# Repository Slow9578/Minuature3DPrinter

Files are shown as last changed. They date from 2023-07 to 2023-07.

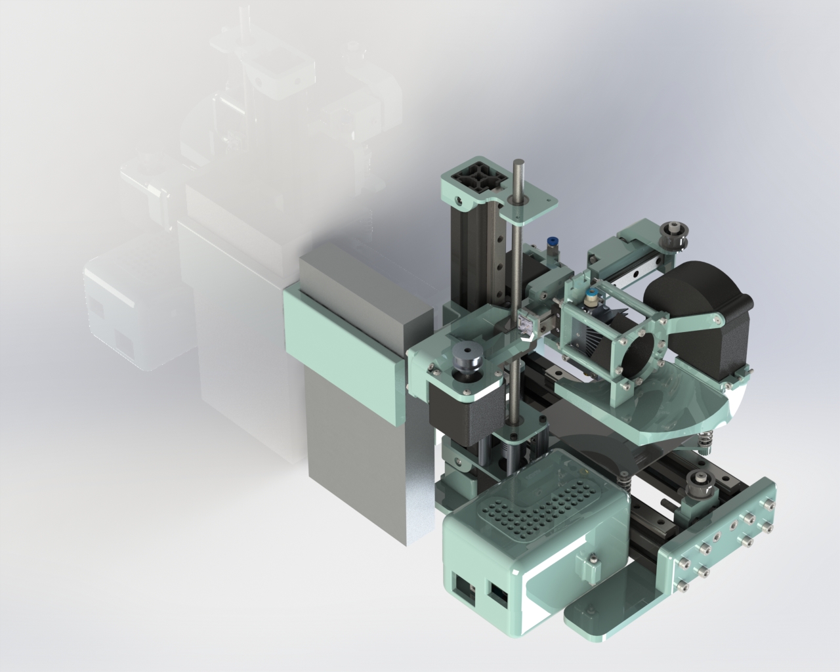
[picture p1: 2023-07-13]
FullCADRenders/PrinterOrthographicView.JPG

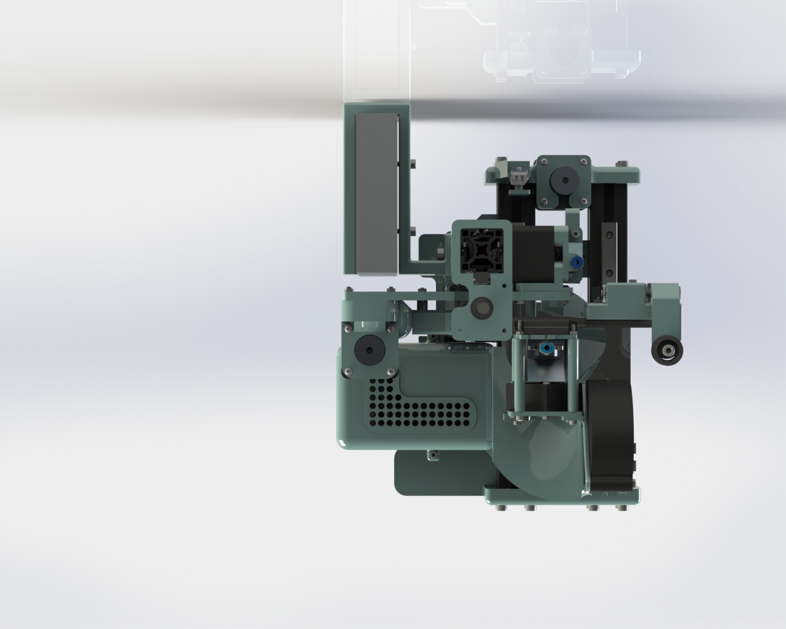
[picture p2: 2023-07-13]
FullCADRenders/PrinterTopView.JPG

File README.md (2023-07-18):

# Minuature3DPrinter
A minuature 3D Printer created for learning more about the inner workings of 3D printers

Due to size constraints the full Solidworks Assembly can be found here:https://drive.google.com/drive/folders/1Yb2QYuJ1OSHzWRYjtjEfcz5mn8uoaapG?usp=sharing

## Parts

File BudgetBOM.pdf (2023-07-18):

Part # | Component | Description | Quantity | Cost Per Unit | Total Cost
HE1A | MK8 HotEnd (https://www.amazon.com/Creality-3D-Assembled-Extruder-Capricorn/dp/B07WNQP916) | Pre-assembled Ender 3 hot end | 1 | 19 | 19
HE2A | Heat Break Fan (https://www.digikey.com/en/products/detail/cui-devices/CFM-4020CF-235-114/15765096) | FAN AXIAL 40X20MM 24VDC WIRE 4.4 CFM | 1 | 6 | 6
HE3A | Print Fan (https://www.amazon.com/Creality-Original-40x40x10MM-Extruder-Printer/dp/B07GXPJB25) | Ender 3 Stock Print Fan | 1 | 9 | 9
HE4A | Mini Heated Bed (https://openbuildspartstore.com/mini-heated-bed/) | 100mm x 100mm 24/12V Openbuild Heated Bed | 1 | 10.99 | 10.99
HE5A | Bed Thermistor (https://www.digikey.com/en/products/detail/littelfuse-inc/GL104R5J/7325040) | THERM NTC 100KOHM 4263K BEAD | 1 | 1.19 | 1.19
HE6A | Bowden Tube (https://www.amazon.com/Creality-Capricorn-Filament-Extruder-Fitting/dp/B09GM6W972) | Bowden PTFE Tube for 1.75mm Filament with Fittings | 1 | 11.45 | 11.45
HW1 | Z-Axis 3030 Aluminum Extrusion (https://www.amazon.com/gp/product/B09FPBK5SP/ref=ox_sc_act_title_1?smid=A2J4PW8EKV80FA&psc=1) | 288.5mm Long, Black Anodized | 1 | 6.66 | 6.66
HW2 | Y-Axis 3030 Aluminum Extrusion (https://www.amazon.com/gp/product/B09FPBK5SP/ref=ox_sc_act_title_1?smid=A2J4PW8EKV80FA&psc=1) | 261mm Long, Black Anodized | 2 | 6.66 | 13.33
HW3 | MGN12H Linear Rail (https://www.amazon.com/gp/product/B08B348GZ9/ref=ox_sc_act_title_2?smid=A1RTFVCI20VZT2&th=1) | 200mm Long | 4 | 13.99 | 55.96
HW4 | 8mm Metric Acme Lead Screw (https://openbuildspartstore.com/8mm-metric-acme-lead-screw/) | 290mm long | 1 | 10.99 | 10.99
HW5 | Anti-Backlash Nut Block (https://openbuildspartstore.com/anti-backlash-nut-block-for-8mm-metric-acme-lead-screw/) | For 8mm Metric Acme Lead Screw | 1 | 9.99 | 9.99
HW6 | 5mm * 8mm Flexible Coupling (https://openbuildspartstore.com/5mm-8mm-flexible-coupling/) | For 8mm Metric Acme Lead Screw | 1 | 6.99 | 6.99
HW7 | Flanged Bearing (https://openbuildspartstore.com/flanged-bearing-688zz-8x16x5/) | 688ZZ 8x16x5 | 2 | 1.5 | 3
HW8 | Timing Belt (https://openbuildspartstore.com/gt2-2m-timing-belt-by-the-foot/) | GT2-2M, 5 Ft. | 1 | 12.45 | 12.45
HW9 | Belt Crimps (https://www.amazon.com/dp/B0968D2GR5?psc=1&ref=ppx_yo2ov_dt_b_product_details) | Copper | 4 | 2.5 | 10
HW10 | Smooth Idler Pulley (https://openbuildspartstore.com/smooth-idler-pulley-kit/) | OD: 22mm ID: 16mm Width: 12.7mm | 2 | 5.99 | 11.98
HW11 | Extruder Drive Gear (https://www.amazon.com/dp/B01J5ON2Y2?psc=1&ref=ppx_yo2ov_dt_b_product_details) | 36Teeth Bore 5mm Stainless Steel Drive Gear | 1 | 6.99 | 6.99
HW12 | Timing Pulley Gear (https://openbuildspartstore.com/gt2-2m-timing-pulley-30-tooth/) | 30 Tooth GT2-2M | 2 | 6.99 | 13.98
HW13 | Bearing Block Spacer (https://openbuildspartstore.com/aluminum-spacers-10-pack/) | M5 ID, 40mm,10mm OD, Aluminum | 4 | 1.5 | 6
HW14 | Extruder Idler Bearing (https://www.amazon.com/uxcell-U604ZZ-Bearings-4mmx13mmx4mm-Shielded/dp/B082PSVNW8?s=industrial) | 4mmx13mmx4mm Double Metal Shielded Carbon Steel Bearings | 1 | 0.66 | 8
E1A | RAMPS 1.4 Sheild (https://www.amazon.com/dp/B01E5K98C6?s=electronics&sp_csd=d2lkZ2V0TmFtZT1zcF9kZXRhaWxfdGhlbWF0aWM) | Shield For Arduino Mega | 1 | 10 | 10
E2A | Arduino Mega (https://www.amazon.com/dp/B08V4RCRS2?psc=1&ref=ppx_yo2ov_dt_b_product_details) | Mega 2560 5V | 1 | 20.99 | 20.99
E3A | 24V Meanwell Power Supply (https://www.mouser.com/ProductDetail/MEAN-WELL/LRS-350-24?qs=ah3jBNVE1PT%252BkwLcackrGA%3D%3D) | LRS-350-24, 24V/14.6A MeanWell Power Suppy | 1 | 37.52 | 37.52
E4A | Stepper Motor Driver (https://www.amazon.com/HiLetgo-Stepstick-Stepper-Printer-Compatible/dp/B07BND65C8?hvadid=616863377916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) | A4988 clones, 5 drivers and 5 heatsinks per 10$ | 4 | 2 | 10
E5A | End Stop Switches (https://mechanicalkeyboards.com/shop/index.php?l=product_detail&p=4117&dqty=1) | Kailh BOX Black Switches Plate Mount - Linear | 3 | 1.16 | 3.5
E6A | Stepper Motor (https://www.amazon.com/Creality-Official-3D-Compatible-axis%EF%BC%88D-Shape%EF%BC%89/dp/B09L5M63B1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) | 42-40 Stepper Motor, 2 Phase 1A 1.8 Degree 0.4 N.M | 4 | 13 | 52
E7A | JST 2Pin Connector Female (https://www.amazon.com/daier-Micro-2-Pin-Connector-Female/dp/B01DUC1O68) | Amazon, 20pcs per 8.99$ | 7 | 0.45 | 8.99
E8A | Stepper Motor Cabels (https://www.amazon.com/Stepper-Cables-Terminal-Paralled-Printer/dp/B08LD14CHS?sp_csd=d2lkZ2V0TmFtZT1zcF9hdGY) | Amazon, 6pcs per 11$ | 4 | 1.83 | 11
P1 | X-AxisBackPlate (https://www.amazon.com/dp/B08ZB48FJM?psc=1&ref=ppx_yo2ov_dt_b_product_details) | 41g PETG, 0.8mm nozzle, 20% infill | 1 | 1.03 | 1.03
P2 | X-AxisMotorFixture (https://www.amazon.com/dp/B08ZB48FJM?psc=1&ref=ppx_yo2ov_dt_b_product_details) | 31g PETG, 0.8mm nozzle, 20% infill | 1 | 0.78 | 0.78
P3A | HotEndBackPlate (https://www.amazon.com/dp/B08ZB48FJM?psc=1&ref=ppx_yo2ov_dt_b_product_details) | 8g PETG, 0.8mm nozzle, 20% infill | 1 | 0.2 | 0.2
P4 | HotEndFrontPlate (https://www.amazon.com/dp/B08ZB48FJM?psc=1&ref=ppx_yo2ov_dt_b_product_details) | 6g PETG, 0.8mm nozzle, 20% infill | 1 | 0.15 | 0.15
P5 | X-AxisBackPlateSpacer (https://www.amazon.com/dp/B08ZB48FJM?psc=1&ref=ppx_yo2ov_dt_b_product_details) | 1g PETG, 0.8mm nozzle, 20% infill | 2 | 0.03 | 0.06

P6 | X-AxisTensionerBase (https://www.amazon.com/dp/B08ZB48FJM?psc=1&ref=ppx_yo2ov_dt_b_product_details) | 40g PETG, 0.8mm nozzle, 20% infill | 1 | 1 | 1
P7 | Y-AxisRailConnectingPlate (https://www.amazon.com/dp/B08ZB48FJM?psc=1&ref=ppx_yo2ov_dt_b_product_details) | 14g PETG, 0.8mm nozzle, 20% infill | 1 | 0.35 | 0.35
P8 | BedBasePlate (https://www.amazon.com/dp/B08ZB48FJM?psc=1&ref=ppx_yo2ov_dt_b_product_details) | 27g PETG, 0.8mm nozzle, 20% infill | 1 | 0.68 | 0.68
P9 | LevelingKnob (https://www.amazon.com/dp/B08ZB48FJM?psc=1&ref=ppx_yo2ov_dt_b_product_details) | 1g PETG, 0.8mm nozzle, 20% infill | 4 | 0.03 | 0.12
P10 | Y-AxisFrontPlate (https://www.amazon.com/dp/B08ZB48FJM?psc=1&ref=ppx_yo2ov_dt_b_product_details) | 42g PETG, 0.8mm nozzle, 20% infill | 1 | 1.05 | 1.05
P11 | BearingPillowBlockPlate (https://www.amazon.com/dp/B08ZB48FJM?psc=1&ref=ppx_yo2ov_dt_b_product_details) | 5g PETG, 0.8mm nozzle, 20% infill | 1 | 0.13 | 0.13
P12 | Z-AxisMotorFixture (https://www.amazon.com/dp/B08ZB48FJM?psc=1&ref=ppx_yo2ov_dt_b_product_details) | 16g PETG, 0.8mm nozzle, 20% infill | 1 | 0.4 | 0.4
P13 | LeadScrewBearingFixture (https://www.amazon.com/dp/B08ZB48FJM?psc=1&ref=ppx_yo2ov_dt_b_product_details) | 16g PETG, 0.8mm nozzle, 20% infill | 1 | 0.4 | 0.4
P14 | Y-AxisRearPlate (https://www.amazon.com/dp/B08ZB48FJM?psc=1&ref=ppx_yo2ov_dt_b_product_details) | 54g PETG, 0.8mm nozzle, 20% infill | 1 | 1.35 | 1.35
P15 | X-AxisTensioner (https://www.amazon.com/dp/B08ZB48FJM?psc=1&ref=ppx_yo2ov_dt_b_product_details) | 13g PETG, 0.8mm nozzle, 20% infill | 1 | 0.33 | 0.33
P16 | ExtruderMotorFixture (https://www.amazon.com/dp/B08ZB48FJM?psc=1&ref=ppx_yo2ov_dt_b_product_details) | 25g PETG, 0.8mm nozzle, 20% infill | 1 | 0.63 | 0.63
P17 | PowerSupplyMountingPlate (https://www.amazon.com/dp/B08ZB48FJM?psc=1&ref=ppx_yo2ov_dt_b_product_details) | 126g PETG, 0.8mm nozzle, 20% infill | 1 | 3.15 | 3.15
P18 | Y-AxisTensioner (https://www.amazon.com/dp/B08ZB48FJM?psc=1&ref=ppx_yo2ov_dt_b_product_details) | 10g PETG, 0.8mm nozzle, 20% infill | 1 | 0.25 | 0.25
P19 | Y-AxisBeltAnchor (https://www.amazon.com/dp/B08ZB48FJM?psc=1&ref=ppx_yo2ov_dt_b_product_details) | 2g PETG, 0.8mm nozzle, 20% infill | 1 | 0.05 | 0.05
P20 | X-AxisEndStop (https://www.amazon.com/dp/B08ZB48FJM?psc=1&ref=ppx_yo2ov_dt_b_product_details) | 5g PETG, 0.8mm nozzle, 20% infill | 1 | 0.13 | 0.13
P21 | HotEndSpacer (https://www.amazon.com/dp/B08ZB48FJM?psc=1&ref=ppx_yo2ov_dt_b_product_details) | 3g PETG, 0.8mm nozzle, 20% infill | 4 | 0.08 | 0.32
P22 | Z-AxisBasePlate (https://www.amazon.com/dp/B08ZB48FJM?psc=1&ref=ppx_yo2ov_dt_b_product_details) | 70g PETG, 0.8mm nozzle, 20% infill | 1 | 1.75 | 1.75
P23A | PrintFanFixture (https://www.amazon.com/dp/B08ZB48FJM?psc=1&ref=ppx_yo2ov_dt_b_product_details) | 6g PETG, 0.8mm nozzle, 20% infill | 1 | 0.15 | 0.15
P25 | Z-AxisEndStopFixture (https://www.amazon.com/dp/B08ZB48FJM?psc=1&ref=ppx_yo2ov_dt_b_product_details) | 3g PETG, 0.8mm nozzle, 20% infill | 1 | 0.08 | 0.08
P26 | Y-AxisEndStopFixture (https://www.amazon.com/dp/B08ZB48FJM?psc=1&ref=ppx_yo2ov_dt_b_product_details) | 10g PETG, 0.8mm nozzle, 20% infill | 1 | 0.25 | 0.25
P27 | FrontBasePlate (https://www.amazon.com/dp/B08ZB48FJM?psc=1&ref=ppx_yo2ov_dt_b_product_details) | 50g PETG, 0.8mm nozzle, 20% infill | 1 | 1.25 | 1.25
P28 | ArduinoCaseBottom (https://www.amazon.com/dp/B08ZB48FJM?psc=1&ref=ppx_yo2ov_dt_b_product_details) | 119g PETG, 0.8mm nozzle, 20% infill | 1 | 2.98 | 2.98
P29 | ArduinoCaseTop (https://www.amazon.com/dp/B08ZB48FJM?psc=1&ref=ppx_yo2ov_dt_b_product_details) | 117g PETG, 0.8mm nozzle, 20% infill | 1 | 2.93 | 2.93
P30 | ArduinoCaseGrate (https://www.amazon.com/dp/B08ZB48FJM?psc=1&ref=ppx_yo2ov_dt_b_product_details) | 10g PETG, 0.8mm nozzle, 20% infill | 1 | 0.25 | 0.25
P31 | Y-Z-AxisConnectingBracket (https://www.amazon.com/dp/B08ZB48FJM?psc=1&ref=ppx_yo2ov_dt_b_product_details) | 7g PETG, 0.8mm nozzle, 20% infill | 1 | 0.18 | 0.18
P32 | ExtruderLever (https://www.amazon.com/dp/B08ZB48FJM?psc=1&ref=ppx_yo2ov_dt_b_product_details) | 7g PETG, 0.8mm nozzle, 20% infill | 1 | 0.18 | 0.18
P33 | ExtruderPlate (https://www.amazon.com/dp/B08ZB48FJM?psc=1&ref=ppx_yo2ov_dt_b_product_details) | 11g PETG, 0.8mm nozzle, 20% infill | 1 | 0.28 | 0.28
P34 | ExtruderSpringEndstop (https://www.amazon.com/dp/B08ZB48FJM?psc=1&ref=ppx_yo2ov_dt_b_product_details) | 1g PETG, 0.8mm nozzle, 20% infill | 1 | 0.03 | 0.03
P35 | EndStopCap (https://www.amazon.com/dp/B08ZB48FJM?psc=1&ref=ppx_yo2ov_dt_b_product_details) | 2g PETG, 0.8mm nozzle, 20% infill | 1 | 0.05 | 0.05
P36 | BacklashNutSpacer (https://www.amazon.com/dp/B08ZB48FJM?psc=1&ref=ppx_yo2ov_dt_b_product_details) | 1g PETG, 0.8mm nozzle, 20% infill | 2 | 0.03 | 0.06
F1A | M3 Socket Head Kit (https://www.amazon.com/1110pcs-Stainless-Washers-Assortment-Precise/dp/B08YYZSZVP) | Contains required fastners F1-F6 and F20 | 1 | 19 | 19
F7 | M3x45mm Socket Head (https://openbuildspartstore.com/m3-cap-head-screws/) | Openbuilds, 1 pc per 0.29$ | 4 | 0.29 | 1.16
F8 | M3x70mm Socket Head (https://www.amazon.com/XunLiu-Socket-Screws-Wrench-Knurled/dp/B07CHKP6F3) | amazon, 10pcs per 8$ | 4 | 1.25 | 8
F2A | M3 Flat Head Kit (https://www.amazon.com/iExcell-Thread-Socket-Screws-Assortment/dp/B08JKCXP9X) | Contains required fastners F9-F12 | 8 | 0.05 | 5.45

F3A | M3 Button Head Kit (https://www.amazon.com/VIGRUE-570PCS-Stainless-Assortment-Machine/dp/B08H24W42K?s=industrial) | Contains required fastners F13-F17 | 1 | 16 | 16
F18 | M3 Set Screw 6mm (https://www.mcmaster.com/91390A100/) | McMaster-Carr:91390A100, $6.52 per pack of 100 | 5 | 0.07 | 6.52
F19 | M3 Tnut (https://openbuildspartstore.com/tee-nuts-m3-10-pack/) | Openbuilds, 10 pcs per 2.79$ | 33 | 0.28 | 11.16
F21 | M4x12mm Socket Head (https://www.amazon.com/M4-0-70-Socket-Screws-Marine-Stainless/dp/B07DVPC7HT) | Amazon, 10pcs per 5.45$ | 2 | 0.55 | 5.45
F22 | M5x6mm Socket Head (https://www.amazon.com/uxcell-M5x6mm-Stainless-Metric-Fasteners/dp/B01IXZ2SSA) | Amazon, 25 pcs per 10$ | 18 | 0.25 | 10
F23 | M5x8mm Socket Head (https://www.amazon.com/Socket-Screws-DIN912-Stainless-M5x18mm/dp/B083DZBVV1) | Amazon, 10pcs per 8$ | 2 | 0.8 | 8
F24 | M5x12mm Socket Head (https://www.amazon.com/Socket-Screws-DIN912-Stainless-M5x18mm/dp/B083DYLJ1S) | Amazon, 10pcs per 8$ | 2 | 0.8 | 8
F25 | M5x18mm Socket Head (https://www.amazon.com/Socket-Screws-DIN912-Stainless-M5x18mm/dp/B083DZDQTH) | Amazon, 10pcs per 8$ | 1 | 0.8 | 8
F26 | M5x40mm LowProfile (https://openbuildspartstore.com/low-profile-screws-m5-10-pack-/) | Openbuilds, 1pcs per 1.69$ | 1 | 1.69 | 1.69
F27 | M5x10mm Flat Head (https://www.amazon.com/METALLIXITY-Countersunk-Machine-M5x10mm-Stainless/dp/B09Y5P8T7W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) | Amazon, 20pcs per 7$ | 1 | 0.35 | 7
F28 | M5x18mm Flat Head (https://www.amazon.com/uxcell-Security-Stainless-Countersunk-Fasteners/dp/B0BC8K7Q1C) | Amazon, 20pcs per 7.50$ | 1 | 0.38 | 7.5
F29 | M5 Tnut (https://openbuildspartstore.com/tee-nuts-m5-10-pack/) | Openbuilds, 10 pcs per $2.99 | 8 | 0.3 | 2.99
F30 | M5 Nut (https://www.mcmaster.com/90592A095/) | McMaster-Carr:90592A095, $4.05 per pack of 100 | 2 | 0.04 | 4.05
F31 | M6x50mm Socket Head (https://www.mcmaster.com/91290A207/) | McMaster-Carr:91290A207, $5.52 per pack of 5 | 4 | 1.1 | 5.52
F32 | M6 Nut (https://www.mcmaster.com/90591A151/) | McMaster-Carr:90591A151, $3.14 per pack of 100 | 4 | 0.03 | 3.14
F33 | Ender3 Bed Spring (https://www.amazon.com/dp/B07FY47BX7?s=industrial&sp_csd=d2lkZ2V0TmFtZT1zcF9kZXRhaWw) | Amazon, 20pcs per 8.99$ | 9 | 0.45 | 8.99
F34 | M3 Heat Inserts (https://www.amazon.com/M3x4-0mm-OD4-6mm-Staking-Threaded-Quik-Tek/dp/B08T7M2H4S) | 100pcs/lot M3x4.0mm, OD4.6mm | 7 | 0.12 | 12
| | | | Total | 570.55

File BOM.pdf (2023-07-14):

Part # | Component | Description | Quantity | Cost Per Unit | Total Cost
HE1 | Aluminum Bar (https://www.mcmaster.com/8975K11-8975K707/) | Multipurpose 6061 Aluminum 1/2" Thick x 1" Wide x 6" Long | 1 | 4.92 | 4.92
HE2 | Volcano nozzle (https://e3d-online.com/products/volcano-nozzles?variant=40924170256443) | Brass E3D Volcano Nozzle 1.75mm in 1.2mm out | 1 | 7.1 | 7.1
HE3 | Heater Cartridge (https://e3d-online.com/products/high-precision-heater-cartridges?variant=31134327504955) | 24V, 40W, E3D High Precision Heater Cartridges | 2 | 20 | 40
HE4 | Heat Sink (https://www.digikey.com/en/products/detail/ohmite/BGAH270-175E/11561718) | BGAH270-175E Heat Sink, 3.5 C/W Natural Thermal Resistance | 1 | 6.61 | 6.61
HE5 | Silicon Casting Kit (https://www.amazon.com/gp/product/B08CVQJ4YD/ref=ppx_yo_dt_b_asin_title_o08_s00?ie=UTF8&psc=1) | Platinum Liquid Silicone for Mold Making | 1 | 34 | 34
HE6 | Heat Break (https://www.amazon.com/gp/product/B09V46R7YR/ref=ppx_yo_dt_b_asin_title_o05_s00?ie=UTF8&psc=1) | Bimetal Heatbreak Titanium Alloy and Copper | 1 | 8.99 | 8.99
HE7 | Bowden Tube (https://www.amazon.com/Creality-Capricorn-Filament-Extruder-Fitting/dp/B09GM6W972) | Bowden PTFE Tube for 1.75mm Filament with Fittings | 1 | 11.45 | 11.45
HE8 | Thermal Paste (https://www.amazon.com/Performance-Ultra-Low-Impedance-Heatsink-Compound/dp/B07KQ1T158) | Corsair TM30 Performance Thermal Paste 0.029 C/W | 1 | 7.99 | 7.99
HE9 | Heat Break Fan (https://www.digikey.com/en/products/detail/cui-devices/CFM-4020CF-235-114/15765096) | FAN AXIAL 40X20MM 24VDC WIRE 4.4 CFM | 1 | 6 | 6
HE10 | Print Fan (https://www.digikey.com/en/products/detail/mechatronics-fan-group/B7530E24B-BSR/5209737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) | FAN BLOWER 76X30MM 24VDC WIRE, B7530E24B-BSR | 1 | 15.8 | 15.8
HE11 | Hot End Thermistor (https://e3d-online.com/products/thermistor-cartridge?_pos=1&_psq=thermi&_ss=e&_v=1.0) | E3D Semitec 104NT Cartridge | 1 | 7 | 7
HE12 | Mini Heated Bed (https://openbuildspartstore.com/mini-heated-bed/) | 100mm x 100mm 24/12V Openbuild Heated Bed | 1 | 10.99 | 10.99
HE13 | PEI Sheet (https://www.amazon.com/gp/product/B07C3GYHYM/ref=ppx_od_dt_b_asin_title_s00?ie=UTF8&psc=1) | Gizmo Dorks PEI Sheet 5" x 5.5" | 1 | 12 | 12
HE14 | Bed Thermistor (https://www.digikey.com/en/products/detail/littelfuse-inc/GL104R5J/7325040) | THERM NTC 100KOHM 4263K BEAD | 1 | 1.19 | 1.19
HW1 | Z-Axis 3030 Aluminum Extrusion (https://www.amazon.com/gp/product/B09FPBK5SP/ref=ox_sc_act_title_1?smid=A2J4PW8EKV80FA&psc=1) | 288.5mm Long, Black Anodized | 1 | 6.66 | 6.66
HW2 | Y-Axis 3030 Aluminum Extrusion (https://www.amazon.com/gp/product/B09FPBK5SP/ref=ox_sc_act_title_1?smid=A2J4PW8EKV80FA&psc=1) | 261mm Long, Black Anodized | 2 | 6.66 | 13.33
HW3 | MGN12H Linear Rail (https://www.amazon.com/gp/product/B08B348GZ9/ref=ox_sc_act_title_2?smid=A1RTFVCI20VZT2&th=1) | 200mm Long | 4 | 13.99 | 55.96
HW4 | 8mm Metric Acme Lead Screw (https://openbuildspartstore.com/8mm-metric-acme-lead-screw/) | 290mm long | 1 | 10.99 | 10.99
HW5 | Anti-Backlash Nut Block (https://openbuildspartstore.com/anti-backlash-nut-block-for-8mm-metric-acme-lead-screw/) | For 8mm Metric Acme Lead Screw | 1 | 9.99 | 9.99
HW6 | 5mm * 8mm Flexible Coupling (https://openbuildspartstore.com/5mm-8mm-flexible-coupling/) | For 8mm Metric Acme Lead Screw | 1 | 6.99 | 6.99
HW7 | Flanged Bearing (https://openbuildspartstore.com/flanged-bearing-688zz-8x16x5/) | 688ZZ 8x16x5 | 2 | 1.5 | 3
HW8 | Timing Belt (https://openbuildspartstore.com/gt2-2m-timing-belt-by-the-foot/) | GT2-2M, 5 Ft. | 1 | 12.45 | 12.45
HW9 | Belt Crimps (https://www.amazon.com/dp/B0968D2GR5?psc=1&ref=ppx_yo2ov_dt_b_product_details) | Copper | 4 | 2.5 | 10
HW10 | Smooth Idler Pulley (https://openbuildspartstore.com/smooth-idler-pulley-kit/) | OD: 22mm ID: 16mm Width: 12.7mm | 2 | 5.99 | 11.98
HW11 | Extruder Drive Gear (https://www.amazon.com/dp/B01J5ON2Y2?psc=1&ref=ppx_yo2ov_dt_b_product_details) | 36Teeth Bore 5mm Stainless Steel Drive Gear | 1 | 6.99 | 6.99
HW12 | Timing Pulley Gear (https://openbuildspartstore.com/gt2-2m-timing-pulley-30-tooth/) | 30 Tooth GT2-2M | 2 | 6.99 | 13.98
HW13 | Bearing Block Spacer (https://openbuildspartstore.com/aluminum-spacers-10-pack/) | M5 ID, 40mm,10mm OD, Aluminum | 4 | 1.5 | 6
HW14 | Extruder Idler Bearing (https://www.amazon.com/uxcell-U604ZZ-Bearings-4mmx13mmx4mm-Shielded/dp/B082PSVNW8?s=industrial) | 4mmx13mmx4mm Double Metal Shielded Carbon Steel Bearings | 1 | 0.66 | 8
E1 | RAMPS 1.4 Sheild (https://www.amazon.com/dp/B01E5K98C6?s=electronics&sp_csd=d2lkZ2V0TmFtZT1zcF9kZXRhaWxfdGhlbWF0aWM) | Shield For Arduino Mega | 1 | 10 | 10
E2 | Arduino Mega (https://www.amazon.com/dp/B08V4RCRS2?psc=1&ref=ppx_yo2ov_dt_b_product_details) | Mega 2560 5V | 1 | 20.99 | 20.99
E3 | 24V Meanwell Power Supply (https://openbuildspartstore.com/24v-meanwell-power-supply-bundle/) | LRS-350-24, 24V/14.6A MeanWell Power Suppy | 1 | 70 | 70

E4 | Stepper Motor Driver (https://www.digikey.com/en/products/detail/pololu-corporation/3099/10450482) | Pololu 3099, 1.1A Continous | 4 | 12.25 | 49
E5 | Stepper Motor Driver Heat Sink (https://www.digikey.com/en/products/detail/watterott-electronic-gmbh/20188/10071165) | SilentStepStick Heatsink 9 x 9 x 12 | 4 | 0.93 | 3.72
E6 | End Stop Switches (https://mechanicalkeyboards.com/shop/index.php?l=product_detail&p=4117&dqty=1) | Kailh BOX Black Switches Plate Mount - Linear | 3 | 1.16 | 3.5
E7 | Stepper Motor (https://www.digikey.com/en/products/detail/sanyo-denki-sanmotion-products/SF2422-10B41/13533492) | SF2422-10B41, Bipolar Stepper Motor Hybrid Frame Size 200.0 Step 1 A 24VDC | 4 | 26 | 104
E8 | JST 2Pin Connector Female (https://www.amazon.com/daier-Micro-2-Pin-Connector-Female/dp/B01DUC1O68) | Amazon, 20pcs per 8.99 | 7 | 0.45 | 8.99
E9 | Stepper Motor Cables (https://www.mouser.com/ProductDetail/SANMOTION/4835775-1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) | SANMOTION 4835775-1 | 4 | 3.75 | 15
E10 | JST 4Pin Connector Female (https://www.amazon.com/Connector-Include-Ph2-0-Female-Ph2-0mm/dp/B08RHGT3W3) | Amazon, 20pcs per 8.59 | 4 | 0.45 | 8.59
P1 | X-AxisBackPlate (https://www.amazon.com/dp/B08ZB48FJM?psc=1&ref=ppx_yo2ov_dt_b_product_details) | 41g PETG, 0.8mm nozzle, 20% infill | 1 | 1.03 | 1.03
P2 | X-AxisMotorFixture (https://www.amazon.com/dp/B08ZB48FJM?psc=1&ref=ppx_yo2ov_dt_b_product_details) | 31g PETG, 0.8mm nozzle, 20% infill | 1 | 0.78 | 0.78
P3 | HotEndBackPlate (https://www.amazon.com/dp/B08ZB48FJM?psc=1&ref=ppx_yo2ov_dt_b_product_details) | 8g PETG, 0.8mm nozzle, 20% infill | 1 | 0.2 | 0.2
P4 | HotEndFrontPlate (https://www.amazon.com/dp/B08ZB48FJM?psc=1&ref=ppx_yo2ov_dt_b_product_details) | 6g PETG, 0.8mm nozzle, 20% infill | 1 | 0.15 | 0.15
P5 | X-AxisBackPlateSpacer (https://www.amazon.com/dp/B08ZB48FJM?psc=1&ref=ppx_yo2ov_dt_b_product_details) | 1g PETG, 0.8mm nozzle, 20% infill | 2 | 0.03 | 0.06
P6 | X-AxisTensionerBase (https://www.amazon.com/dp/B08ZB48FJM?psc=1&ref=ppx_yo2ov_dt_b_product_details) | 40g PETG, 0.8mm nozzle, 20% infill | 1 | 1 | 1
P7 | Y-AxisRailConnectingPlate (https://www.amazon.com/dp/B08ZB48FJM?psc=1&ref=ppx_yo2ov_dt_b_product_details) | 14g PETG, 0.8mm nozzle, 20% infill | 1 | 0.35 | 0.35
P8 | BedBasePlate (https://www.amazon.com/dp/B08ZB48FJM?psc=1&ref=ppx_yo2ov_dt_b_product_details) | 27g PETG, 0.8mm nozzle, 20% infill | 1 | 0.68 | 0.68
P9 | LevelingKnob (https://www.amazon.com/dp/B08ZB48FJM?psc=1&ref=ppx_yo2ov_dt_b_product_details) | 1g PETG, 0.8mm nozzle, 20% infill | 4 | 0.03 | 0.12
P10 | Y-AxisFrontPlate (https://www.amazon.com/dp/B08ZB48FJM?psc=1&ref=ppx_yo2ov_dt_b_product_details) | 42g PETG, 0.8mm nozzle, 20% infill | 1 | 1.05 | 1.05
P11 | BearingPillowBlockPlate (https://www.amazon.com/dp/B08ZB48FJM?psc=1&ref=ppx_yo2ov_dt_b_product_details) | 5g PETG, 0.8mm nozzle, 20% infill | 1 | 0.13 | 0.13
P12 | Z-AxisMotorFixture (https://www.amazon.com/dp/B08ZB48FJM?psc=1&ref=ppx_yo2ov_dt_b_product_details) | 16g PETG, 0.8mm nozzle, 20% infill | 1 | 0.4 | 0.4
P13 | LeadScrewBearingFixture (https://www.amazon.com/dp/B08ZB48FJM?psc=1&ref=ppx_yo2ov_dt_b_product_details) | 16g PETG, 0.8mm nozzle, 20% infill | 1 | 0.4 | 0.4
P14 | Y-AxisRearPlate (https://www.amazon.com/dp/B08ZB48FJM?psc=1&ref=ppx_yo2ov_dt_b_product_details) | 54g PETG, 0.8mm nozzle, 20% infill | 1 | 1.35 | 1.35
P15 | X-AxisTensioner (https://www.amazon.com/dp/B08ZB48FJM?psc=1&ref=ppx_yo2ov_dt_b_product_details) | 13g PETG, 0.8mm nozzle, 20% infill | 1 | 0.33 | 0.33
P16 | ExtruderMotorFixture (https://www.amazon.com/dp/B08ZB48FJM?psc=1&ref=ppx_yo2ov_dt_b_product_details) | 25g PETG, 0.8mm nozzle, 20% infill | 1 | 0.63 | 0.63
P17 | PowerSupplyMountingPlate (https://www.amazon.com/dp/B08ZB48FJM?psc=1&ref=ppx_yo2ov_dt_b_product_details) | 126g PETG, 0.8mm nozzle, 20% infill | 1 | 3.15 | 3.15
P18 | Y-AxisTensioner (https://www.amazon.com/dp/B08ZB48FJM?psc=1&ref=ppx_yo2ov_dt_b_product_details) | 10g PETG, 0.8mm nozzle, 20% infill | 1 | 0.25 | 0.25
P19 | Y-AxisBeltAnchor (https://www.amazon.com/dp/B08ZB48FJM?psc=1&ref=ppx_yo2ov_dt_b_product_details) | 2g PETG, 0.8mm nozzle, 20% infill | 1 | 0.05 | 0.05
P20 | X-AxisEndStop (https://www.amazon.com/dp/B08ZB48FJM?psc=1&ref=ppx_yo2ov_dt_b_product_details) | 5g PETG, 0.8mm nozzle, 20% infill | 1 | 0.13 | 0.13
P21 | HotEndSpacer (https://www.amazon.com/dp/B08ZB48FJM?psc=1&ref=ppx_yo2ov_dt_b_product_details) | 3g PETG, 0.8mm nozzle, 20% infill | 4 | 0.08 | 0.32
P22 | Z-AxisBasePlate (https://www.amazon.com/dp/B08ZB48FJM?psc=1&ref=ppx_yo2ov_dt_b_product_details) | 70g PETG, 0.8mm nozzle, 20% infill | 1 | 1.75 | 1.75
P23 | PrintFanFixture (https://www.amazon.com/dp/B08ZB48FJM?psc=1&ref=ppx_yo2ov_dt_b_product_details) | 6g PETG, 0.8mm nozzle, 20% infill | 1 | 0.15 | 0.15
P24 | FanDuct (https://www.amazon.com/dp/B08ZB48FJM?psc=1&ref=ppx_yo2ov_dt_b_product_details) | 102g PETG, 0.8mm nozzle, 20% infill | 1 | 2.55 | 2.55
P25 | Z-AxisEndStopFixture (https://www.amazon.com/dp/B08ZB48FJM?psc=1&ref=ppx_yo2ov_dt_b_product_details) | 3g PETG, 0.8mm nozzle, 20% infill | 1 | 0.08 | 0.08
P26 | Y-AxisEndStopFixture (https://www.amazon.com/dp/B08ZB48FJM?psc=1&ref=ppx_yo2ov_dt_b_product_details) | 10g PETG, 0.8mm nozzle, 20% infill | 1 | 0.25 | 0.25
P27 | FrontBasePlate (https://www.amazon.com/dp/B08ZB48FJM?psc=1&ref=ppx_yo2ov_dt_b_product_details) | 50g PETG, 0.8mm nozzle, 20% infill | 1 | 1.25 | 1.25

P28 | ArduinoCaseBottom (https://www.amazon.com/dp/B08ZB48FJM?psc=1&ref=ppx_yo2ov_dt_b_product_details) | 119g PETG, 0.8mm nozzle, 20% infill | 1 | 2.98 | 2.98
P29 | ArduinoCaseTop (https://www.amazon.com/dp/B08ZB48FJM?psc=1&ref=ppx_yo2ov_dt_b_product_details) | 117g PETG, 0.8mm nozzle, 20% infill | 1 | 2.93 | 2.93
P30 | ArduinoCaseGrate (https://www.amazon.com/dp/B08ZB48FJM?psc=1&ref=ppx_yo2ov_dt_b_product_details) | 10g PETG, 0.8mm nozzle, 20% infill | 1 | 0.25 | 0.25
P31 | Y-Z-AxisConnectingBracket (https://www.amazon.com/dp/B08ZB48FJM?psc=1&ref=ppx_yo2ov_dt_b_product_details) | 7g PETG, 0.8mm nozzle, 20% infill | 1 | 0.18 | 0.18
P32 | ExtruderLever (https://www.amazon.com/dp/B08ZB48FJM?psc=1&ref=ppx_yo2ov_dt_b_product_details) | 7g PETG, 0.8mm nozzle, 20% infill | 1 | 0.18 | 0.18
P33 | ExtruderPlate (https://www.amazon.com/dp/B08ZB48FJM?psc=1&ref=ppx_yo2ov_dt_b_product_details) | 11g PETG, 0.8mm nozzle, 20% infill | 1 | 0.28 | 0.28
P34 | ExtruderSpringEndstop (https://www.amazon.com/dp/B08ZB48FJM?psc=1&ref=ppx_yo2ov_dt_b_product_details) | 1g PETG, 0.8mm nozzle, 20% infill | 1 | 0.03 | 0.03
P35 | EndStopCap (https://www.amazon.com/dp/B08ZB48FJM?psc=1&ref=ppx_yo2ov_dt_b_product_details) | 2g PETG, 0.8mm nozzle, 20% infill | 1 | 0.05 | 0.05
P36 | BacklashNutSpacer (https://www.amazon.com/dp/B08ZB48FJM?psc=1&ref=ppx_yo2ov_dt_b_product_details) | 1g PETG, 0.8mm nozzle, 20% infill | 2 | 0.03 | 0.06
F1 | M3x10mm Socket Head (https://www.mcmaster.com/91290A115/) | McMaster-Carr: 91290A115, $9.54 per pack of 100 | 4 | 0.1 | 9.54
F2 | M3x12mm Socket Head (https://www.mcmaster.com/91290A117/) | McMaster-Carr:91290A117, $10.85 per pack of 100 | 5 | 0.11 | 10.85
F3 | M3x16mm Socket Head (https://www.mcmaster.com/91290A120/) | McMaster-Carr:91290A120, $11.48 per pack of 100 | 1 | 0.11 | 11.48
F4 | M3x20mm Socket Head (https://www.mcmaster.com/91290A123/) | McMaster-Carr:91290A123, $13.59 per pack of 100 | 5 | 0.14 | 13.59
F5 | M3x25mm Socket Head (https://www.mcmaster.com/91290A125/) | McMaster-Carr:91290A125, $16.70 per pack of 100 | 7 | 0.17 | 16.7
F6 | M3x30mm Socket Head (https://www.mcmaster.com/91290A171/) | McMaster-Carr:91290A171, $7.17 per pack of 10 | 1 | 0.72 | 7.17
F7 | M3x45mm Socket Head (https://openbuildspartstore.com/m3-cap-head-screws/) | Openbuilds, 1 pc per 0.29$ | 4 | 0.29 | 1.16
F8 | M3x70mm Socket Head (https://www.mcmaster.com/91290A297/) | McMaster-Carr:91290A297, $4.26 per pack of 1 | 4 | 4.26 | 17.04
F9 | M3x6mm Flat Head (https://www.mcmaster.com/91294A126/) | McMaster-Carr:91294A126, $5.45 per pack of 100 | 8 | 0.05 | 5.45
F10 | M3x12mm Flat Head (https://www.mcmaster.com/91294A132/) | McMaster-Carr:91294A132, $7.34 per pack of 100 | 1 | 0.07 | 7.34
F11 | M3x30mm Flat Head (https://www.mcmaster.com/91294A141/) | McMaster-Carr:91294A141, $6.93 per pack of 50 | 7 | 0.04 | 6.93
F12 | M3x35mm Flat Head (https://www.mcmaster.com/91294A536/) | McMaster-Carr:91294A536, $13.17 per pack of 25 | 2 | 0.53 | 13.17
F13 | M3x6mm Button Head (https://openbuildspartstore.com/button-head-screws-m3-25-pack/) | Openbuilds, 10 pcs per 1$ | 1 | 0.1 | 1
F14 | M3x8mm Button Head (https://openbuildspartstore.com/button-head-screws-m3-25-pack/) | Openbuilds, 10 pcs per 1$ | 41 | 0.1 | 5
F15 | M3x12mm Button Head (https://openbuildspartstore.com/button-head-screws-m3-25-pack/) | Openbuilds, 10 pcs per 1$ | 6 | 0.1 | 1
F16 | M3x18mm Button Head (https://www.mcmaster.com/92095A472/) | McMaster-Carr:92095A472, $8.70 per pack of 100 | 2 | 0.09 | 8.7
F17 | M3x25mm Button Head (https://www.mcmaster.com/92095A186/) | McMaster-Carr:92095A186, $6.34 per pack of 50 | 4 | 0.13 | 6.34
F18 | M3 Set Screw 6mm (https://www.mcmaster.com/91390A100/) | McMaster-Carr:91390A100, $6.52 per pack of 100 | 5 | 0.07 | 6.52
F19 | M3 Tnut (https://openbuildspartstore.com/tee-nuts-m3-10-pack/) | Openbuilds, 10 pcs per 2.79$ | 33 | 0.28 | 11.16
F20 | M3 Nut (https://www.mcmaster.com/90592A085/) | McMaster-Carr:90592A085, $2.62 per pack of 100 | 32 | 0.03 | 2.62
F21 | M4x12mm Socket Head (https://www.mcmaster.com/91290A148/) | McMaster-Carr:91290A148, $11.54 per pack of 100 | 2 | 0.12 | 11.54
F22 | M5x6mm Socket Head (https://www.mcmaster.com/91290A221/) | McMaster-Carr:91290A221, $13.12 per pack of 100 | 18 | 0.13 | 13.12
F23 | M5x8mm Socket Head (https://www.mcmaster.com/91290A222/) | McMaster-Carr:91290A222, $12.28 per pack of 100 | 2 | 0.13 | 12.28
F24 | M5x12mm Socket Head (https://www.mcmaster.com/91290A228/) | McMaster-Carr:91290A228, $15.38 per pack of 100 | 2 | 0.15 | 15.38
F25 | M5x18mm Socket Head (https://www.mcmaster.com/91290A238/) | McMaster-Carr:91290A238, $17.44 per pack of 100 | 1 | 0.17 | 17.44

F26 | M5x40mm LowProfile (https://www.mcmaster.com/93070A133/) | McMaster-Carr:93070A133, $8.18 per pack of 25 | 1 | 0.33 | 8.18
F27 | M5x10mm Flat Head (https://www.mcmaster.com/92125A208/) | McMaster-Carr:92125A208, $14.76 per pack of 100 | 1 | 0.15 | 14.76
F28 | M5x18mm Flat Head (https://www.mcmaster.com/92125A213/) | McMaster-Carr:92125A213, $10.62 per pack of 50 | 1 | 0.21 | 10.62
F29 | M5 Tnut (https://openbuildspartstore.com/tee-nuts-m5-10-pack/) | Openbuilds, 10 pcs per $2.99 | 8 | 0.3 | 2.99
F30 | M5 Nut (https://www.mcmaster.com/90592A095/) | McMaster-Carr:90592A095, $4.05 per pack of 100 | 2 | 0.04 | 4.05
F31 | M6x50mm Socket Head (https://www.mcmaster.com/91290A207/) | McMaster-Carr:91290A207, $5.52 per pack of 5 | 4 | 1.1 | 5.52
F32 | M6 Nut (https://www.mcmaster.com/90591A151/) | McMaster-Carr:90591A151, $3.14 per pack of 100 | 4 | 0.03 | 3.14
F33 | Ender3 Bed Spring (https://www.amazon.com/dp/B07FY47BX7?s=industrial&sp_csd=d2lkZ2V0TmFtZT1zcF9kZXRhaWw) | Amazon, 20pcs per 8.99 | 9 | 0.45 | 8.99
F34 | M3 Heat Inserts (https://www.amazon.com/M3x4-0mm-OD4-6mm-Staking-Threaded-Quik-Tek/dp/B08T7M2H4S) | 100pcs/lot M3x4.0mm, OD4.6mm | 7 | 0.12 | 12
| | | | Total | 972.45

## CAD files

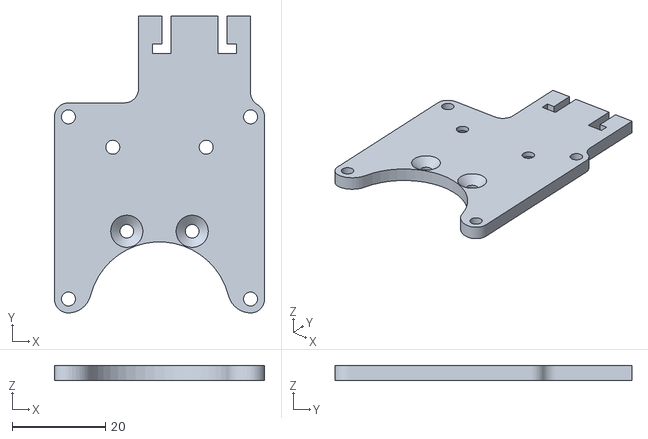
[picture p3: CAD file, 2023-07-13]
Printable Component STLs/Ender3HotEndComponents/HotEndBackPlate.STL
45.0 x 63.6 x 3.17

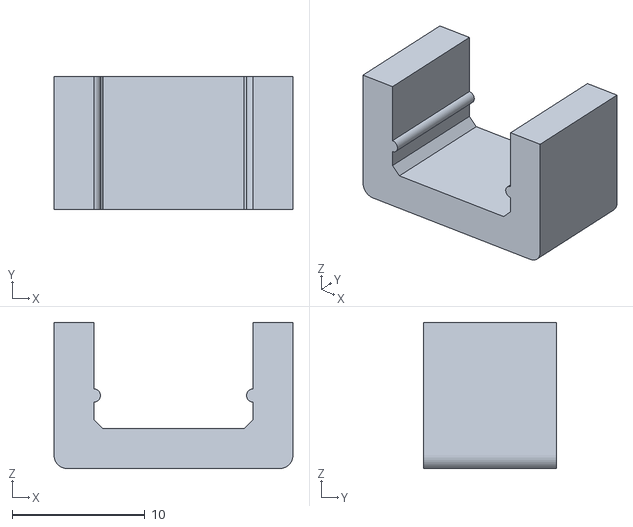
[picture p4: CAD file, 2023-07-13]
Printable Component STLs/ExtraComponents/LinearRailEndStop.STL
18.0 x 10.0 x 11.0

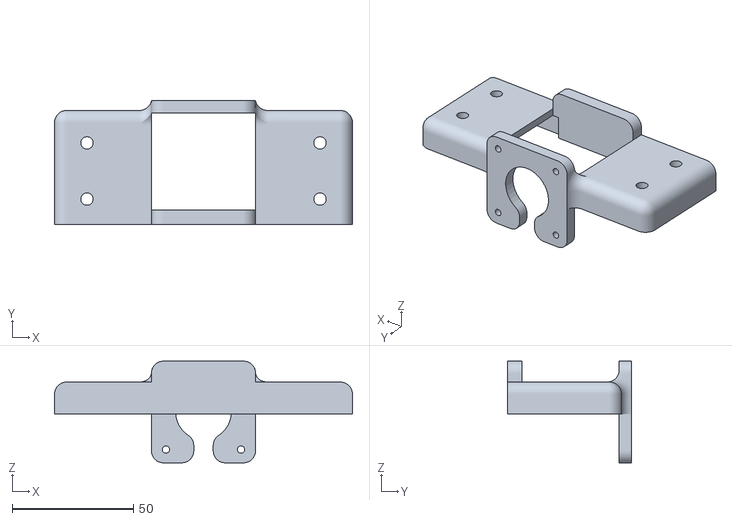
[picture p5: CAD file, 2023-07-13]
Printable Component STLs/Y-AxisBackPlate.STL
123.0 x 51.0 x 42.0

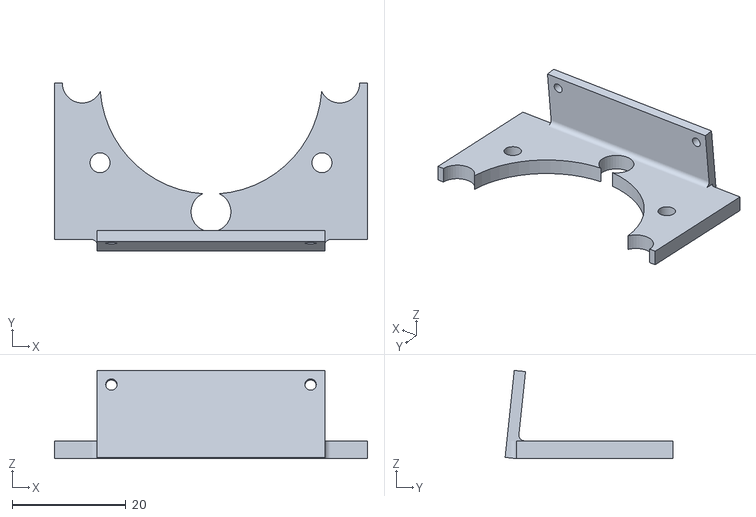
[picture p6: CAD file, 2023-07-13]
Printable Component STLs/Ender3HotEndComponents/PrintFanFixture.STL
55.0 x 29.5 x 15.5

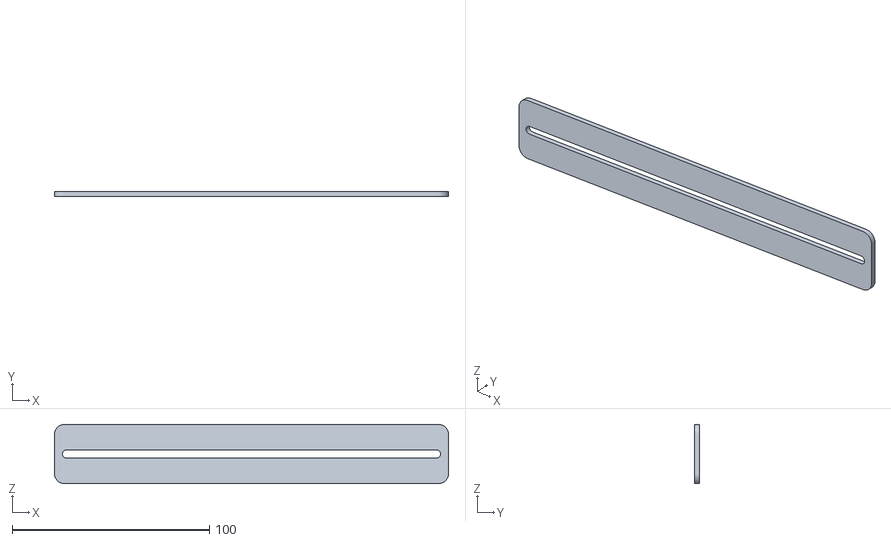
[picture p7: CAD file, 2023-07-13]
Printable Component STLs/ExtraComponents/TslotCover.STL
200.0 x 2.40 x 30.0

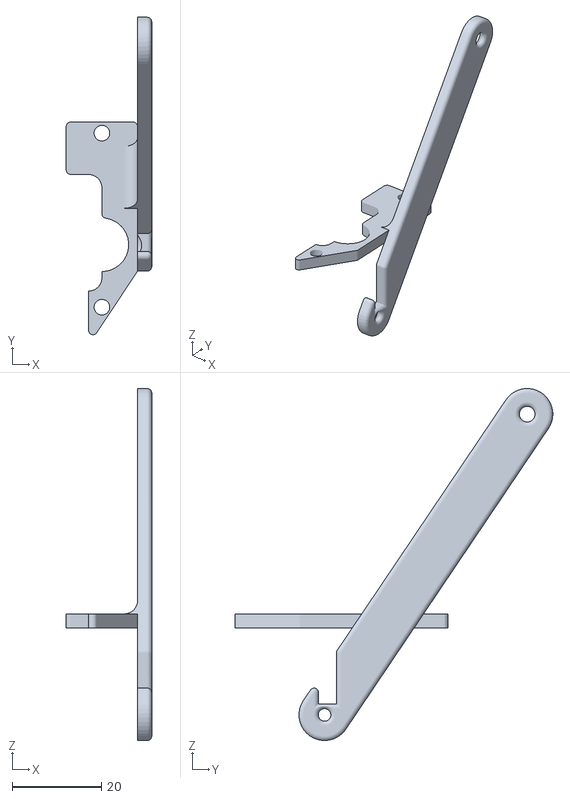
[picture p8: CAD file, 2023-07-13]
Printable Component STLs/PrintFanFixture.STL
19.2 x 71.2 x 78.9

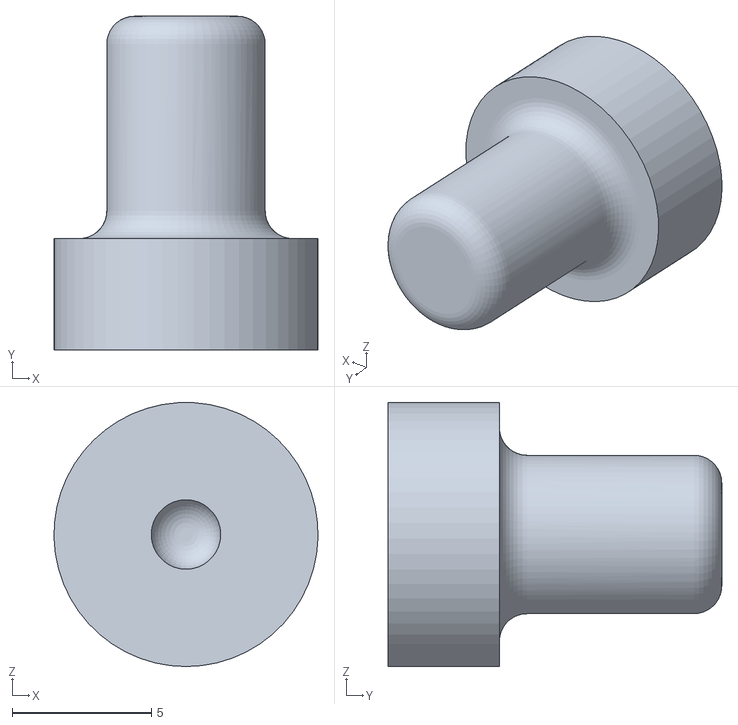
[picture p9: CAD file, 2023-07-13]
Printable Component STLs/ExtruderSpringEndstop.STL
9.50 x 12.0 x 9.50

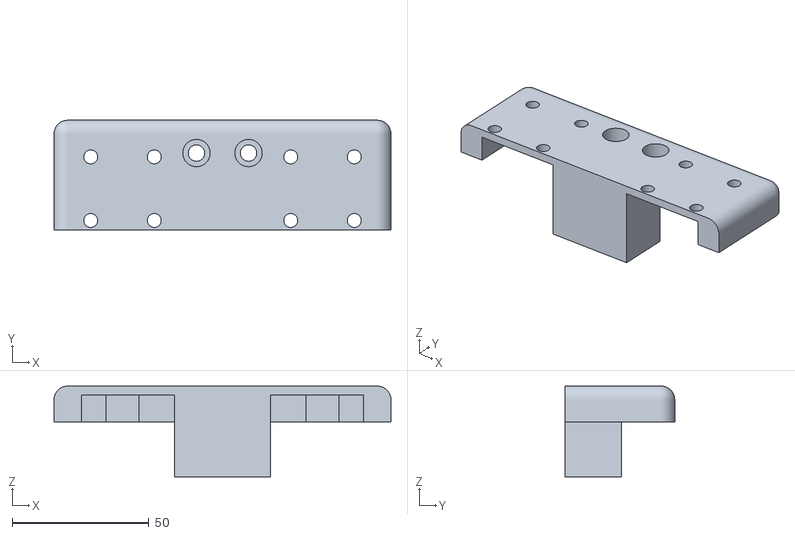
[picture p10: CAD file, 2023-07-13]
Printable Component STLs/Y-AxisFrontPlate.STL
123.0 x 40.0 x 33.2

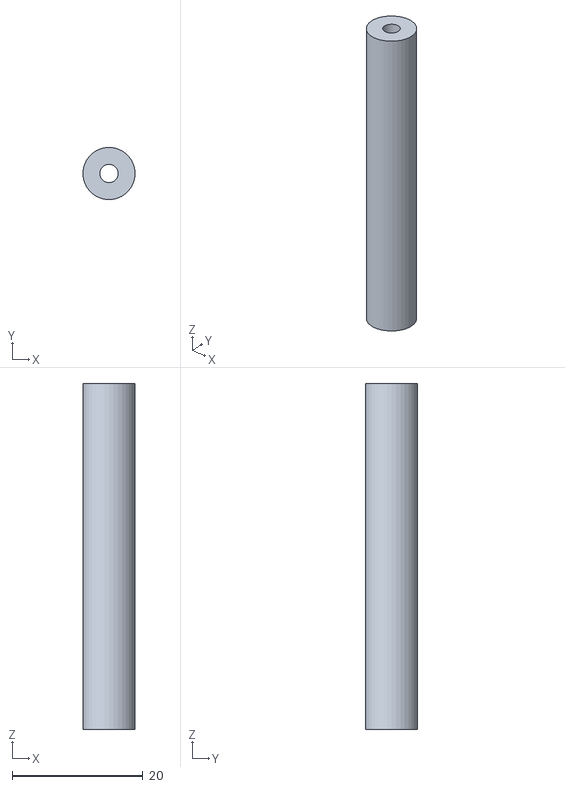
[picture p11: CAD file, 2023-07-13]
Printable Component STLs/HotEndSpacer.STL
8.00 x 8.00 x 53.0

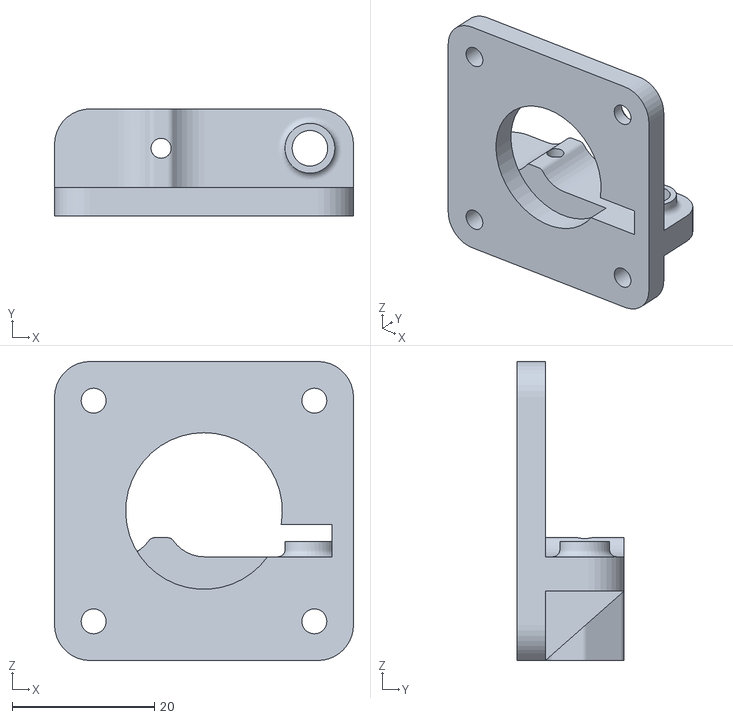
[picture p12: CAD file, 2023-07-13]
Printable Component STLs/ExtruderPlate.STL
42.0 x 15.1 x 42.0

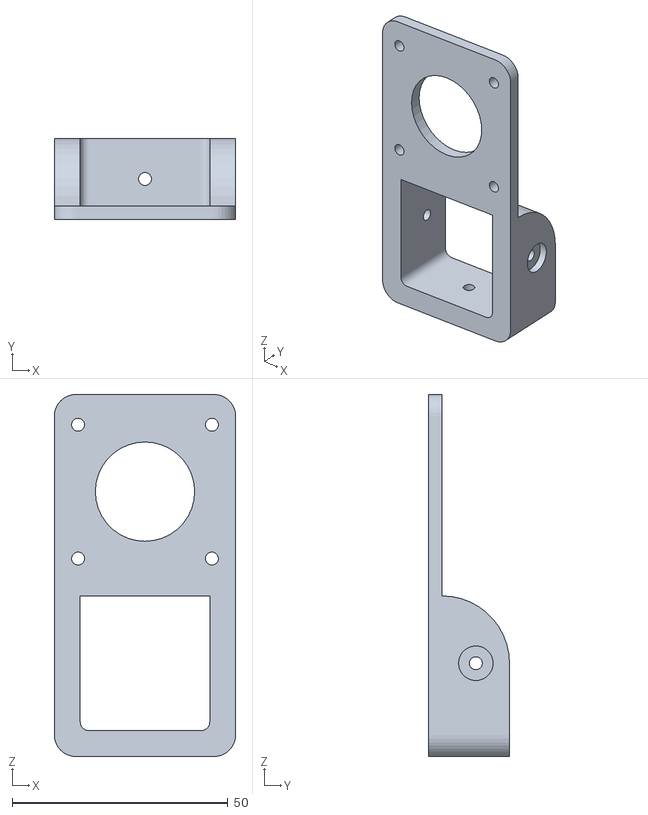
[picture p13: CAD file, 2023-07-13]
Printable Component STLs/Z-AxisMotorFixture.STL
42.0 x 18.8 x 83.8

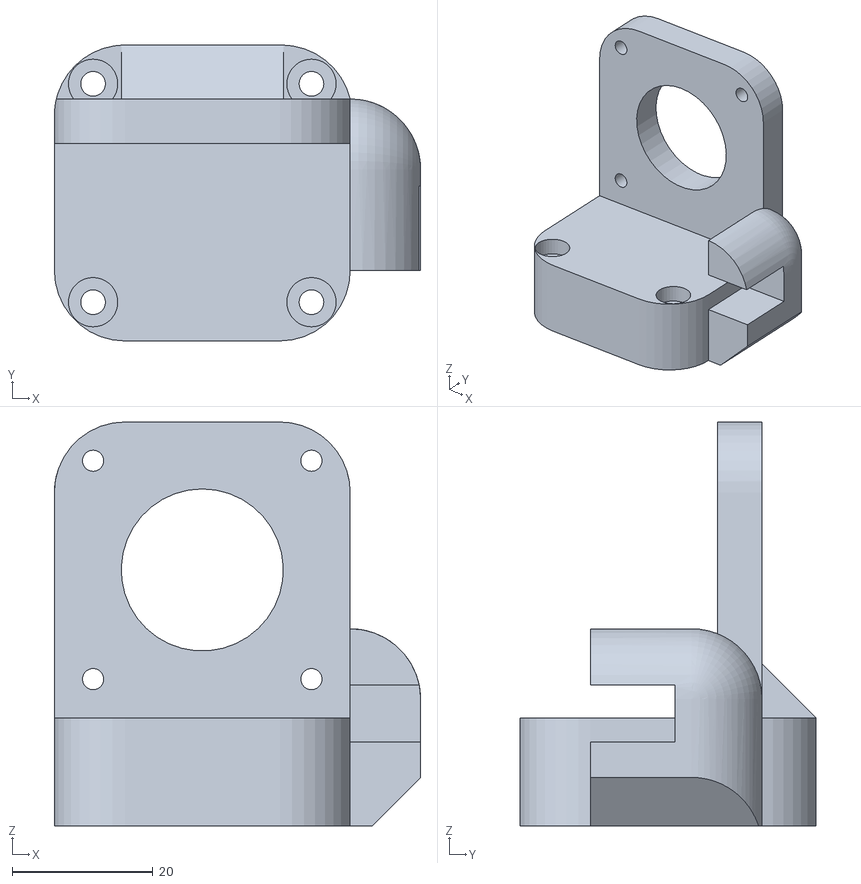
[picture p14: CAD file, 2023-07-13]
Printable Component STLs/X-AxisMotorFixture.STL
52.0 x 42.0 x 57.3

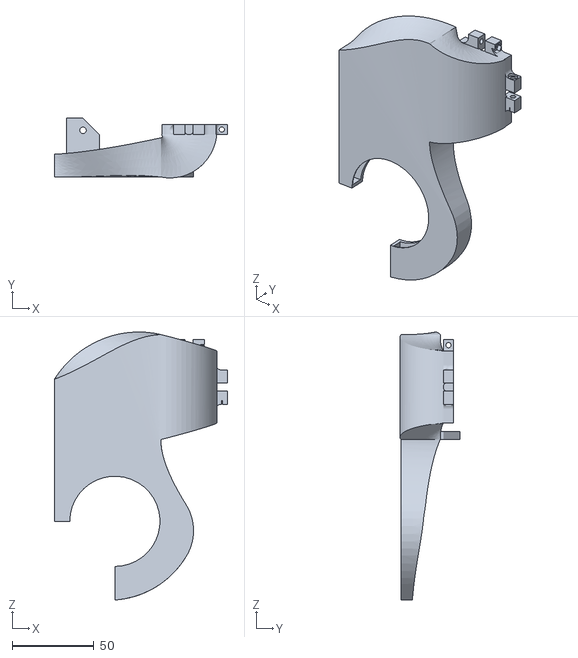
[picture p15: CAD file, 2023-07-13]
Printable Component STLs/FanDuct.STL
105.6 x 36.5 x 163.5

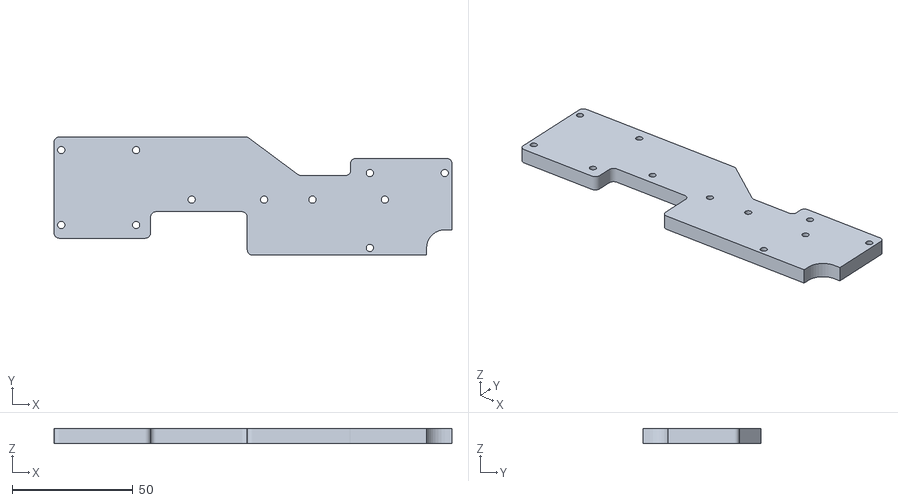
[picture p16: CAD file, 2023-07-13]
Printable Component STLs/X-AxisBackPlate.STL
164.8 x 49.0 x 6.35

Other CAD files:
Printable Component STLs/ExtruderMotorFixture.STL
Printable Component STLs/X-AxisTensioner.STL
Printable Component STLs/Y-AxisEndStopFixture.STL
Printable Component STLs/ExtruderLever.STL
Printable Component STLs/BacklashNutSpacer.STL
Printable Component STLs/BearingPillowBlockPlate.STL
Printable Component STLs/BedBasePlate.STL
Printable Component STLs/EndStopCap.STL
Printable Component STLs/FrontBasePlate.STL
Printable Component STLs/HotEndBackPlate.STL
Printable Component STLs/HotEndFrontPlate.STL
Printable Component STLs/LeadScrewBearingFixture.STL
Printable Component STLs/LevelingKnob.STL
Printable Component STLs/PowerSupplyMountingPlate.STL
Printable Component STLs/X-AxisBackPlateSpacer.STL
Printable Component STLs/X-AxisEndStop.STL
Printable Component STLs/X-AxisTensionerBase.STL
Printable Component STLs/Y-AxisBeltAnchor.STL
Printable Component STLs/Y-AxisRailConnectingPlate.STL
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

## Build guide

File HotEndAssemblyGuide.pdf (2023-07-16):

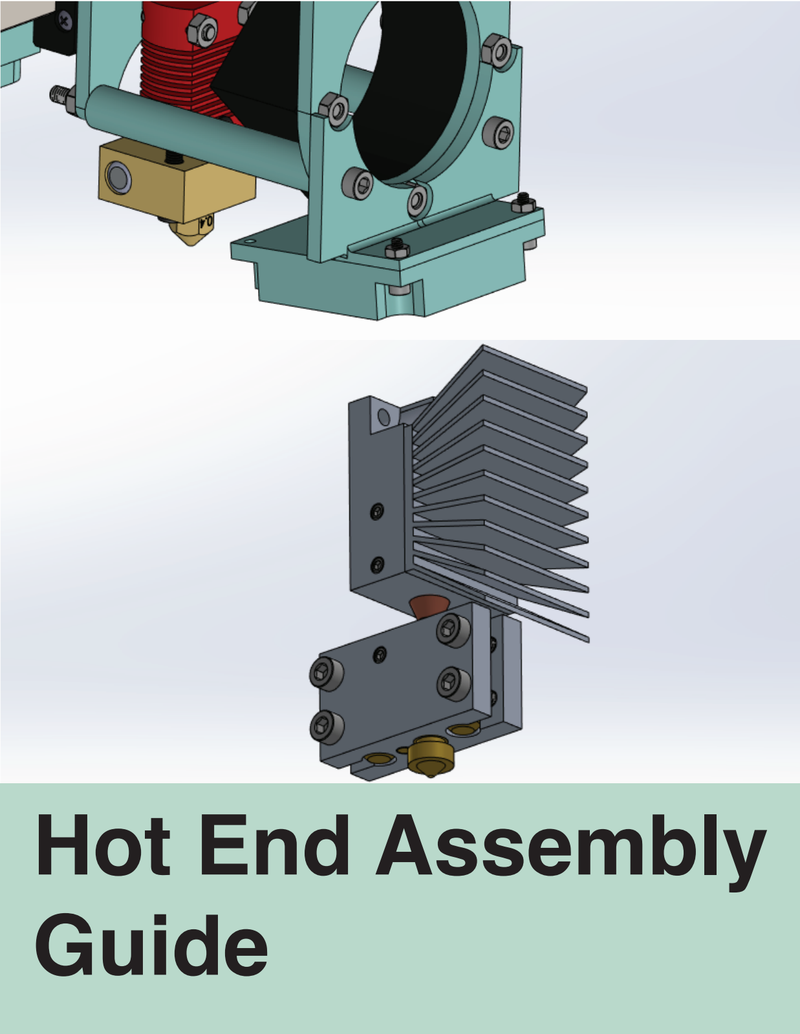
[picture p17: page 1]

# Hot End Assembly Guide

# Table of Contents

## Components

## Hot End Assembly

## Non Custom Assembly

3

4-16

17-22

## HE1 Heat Break Block HE2 Heater Block HE3 Heat Break HE4 Heat Sink HE5 Heater Cartridge HE6 Nozzle HE7 Thermistor HE8 Thermal Paste HE9 Set Screws HE10 M3x12mm

# Components

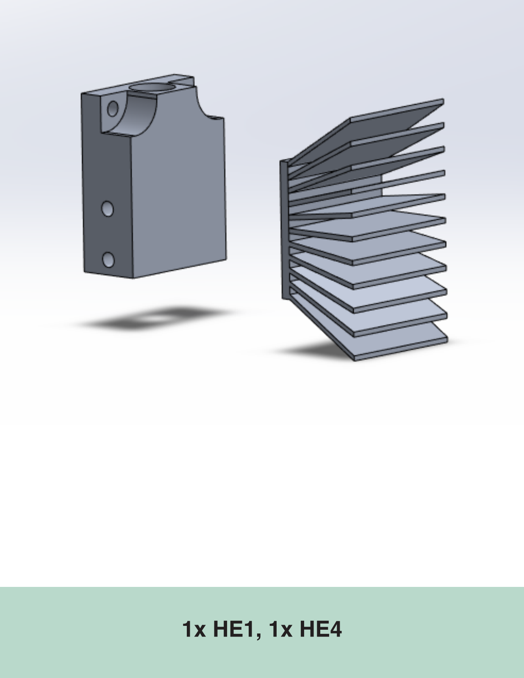
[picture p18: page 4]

1x HE1, 1x HE4

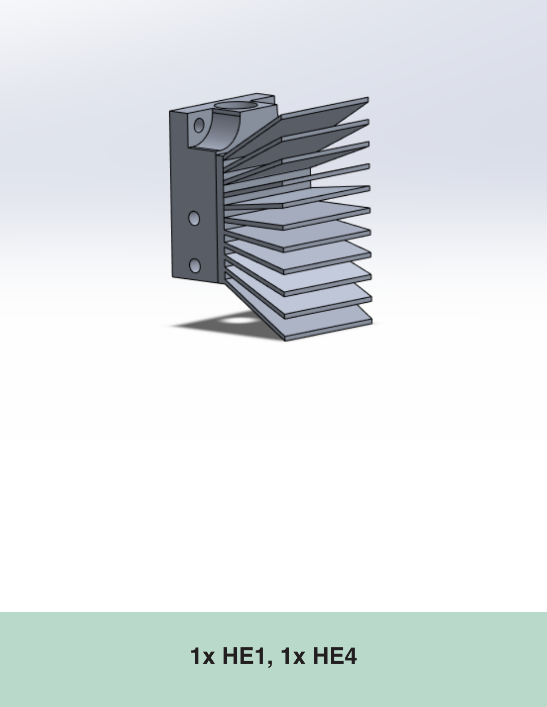
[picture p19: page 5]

1x HE1, 1x HE4

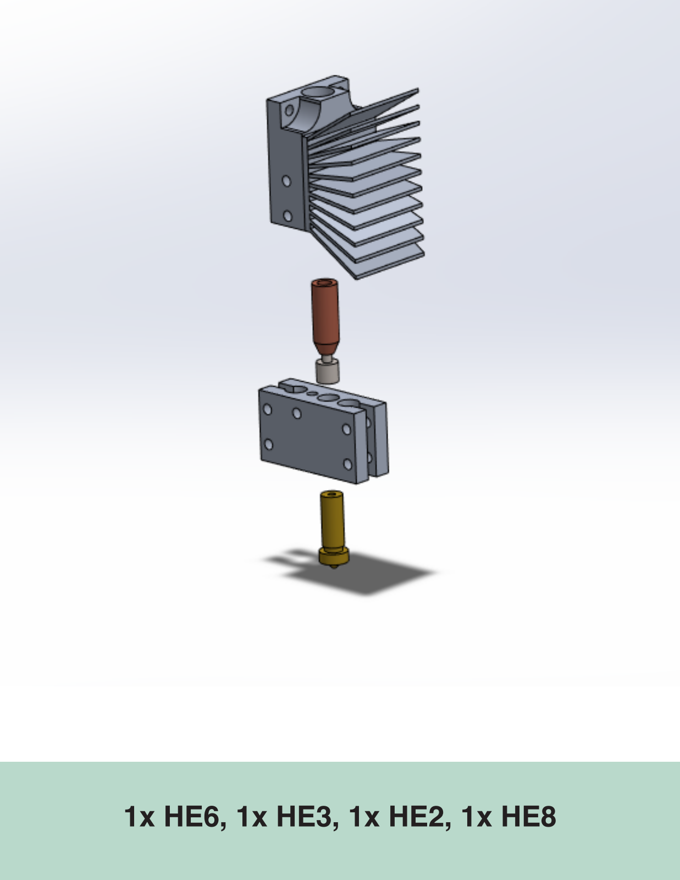
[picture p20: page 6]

1x HE6, 1x HE3, 1x HE2, 1x HE8

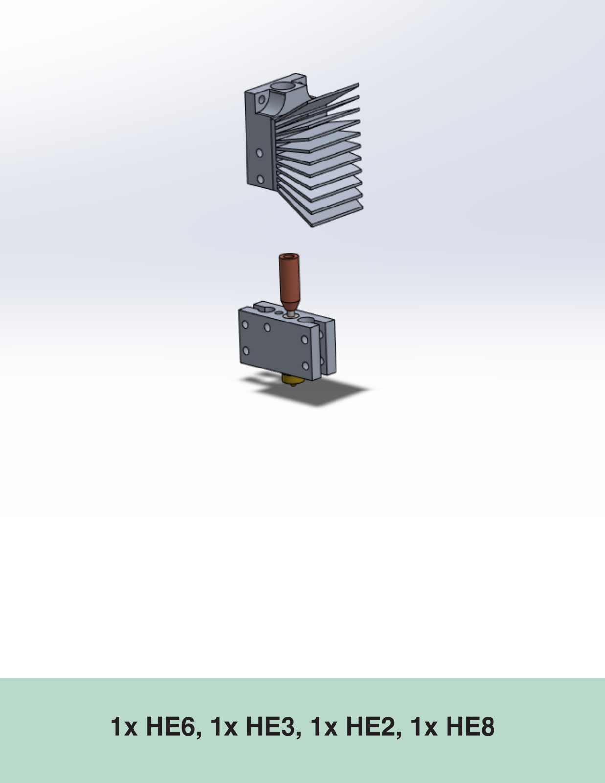
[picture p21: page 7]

1x HE6, 1x HE3, 1x HE2, 1x HE8

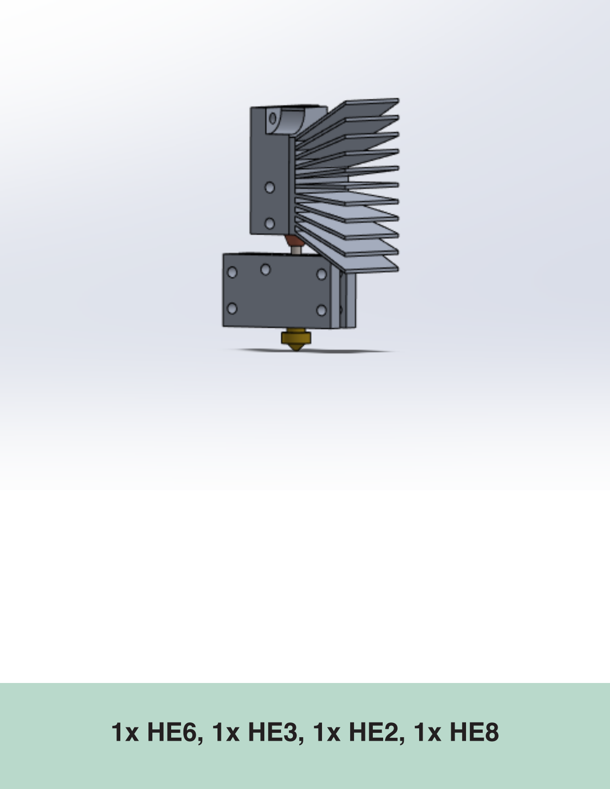
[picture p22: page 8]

1x HE6, 1x HE3, 1x HE2, 1x HE8

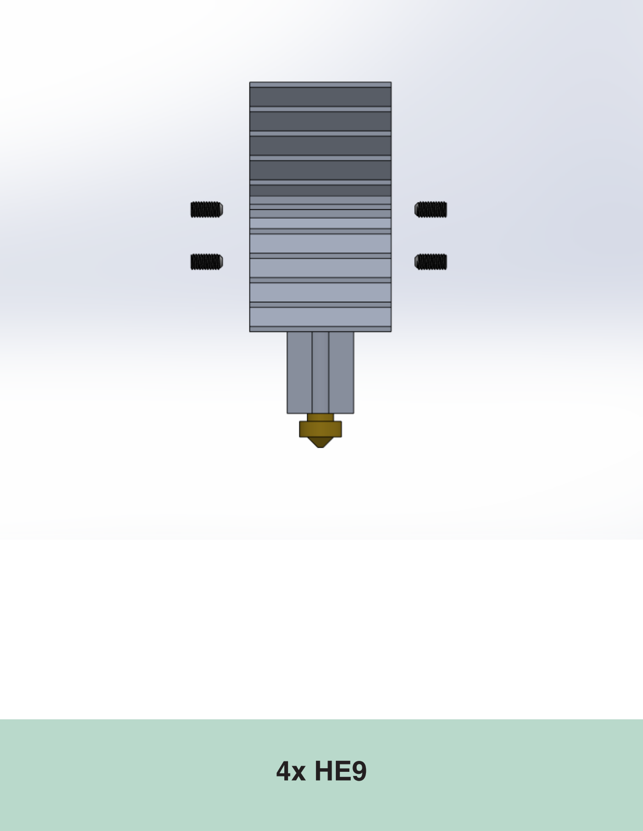
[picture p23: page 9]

4x HE9

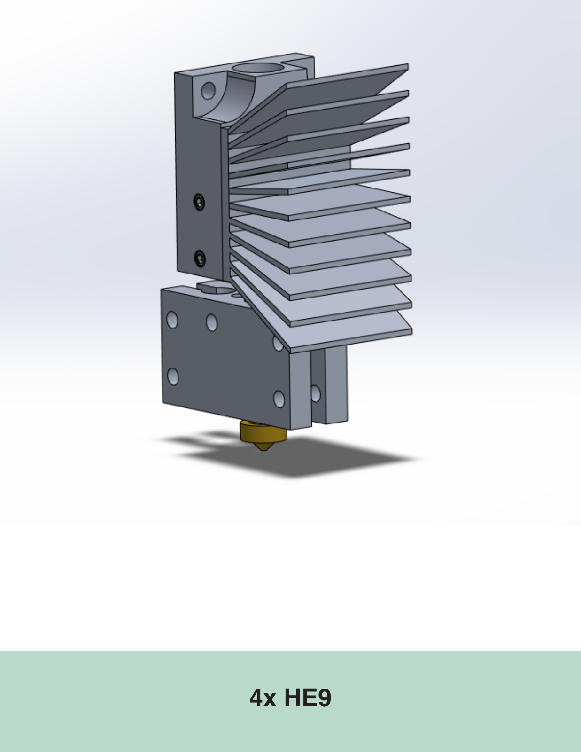
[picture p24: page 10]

4x HE9

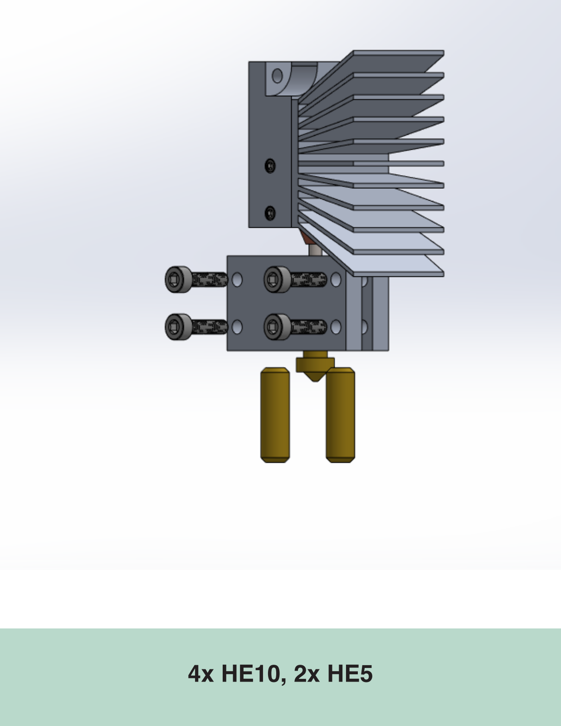
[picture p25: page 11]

4x HE10, 2x HE5

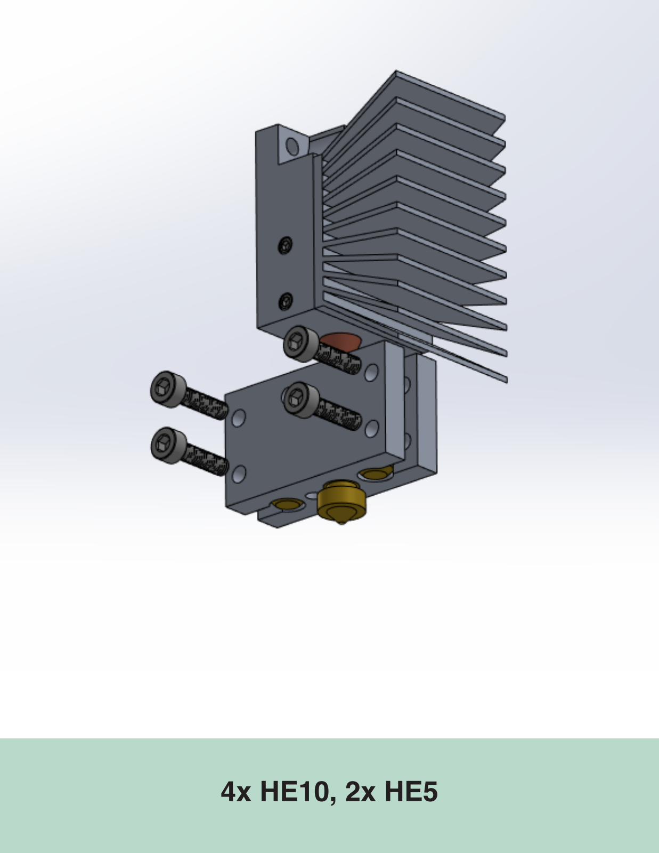
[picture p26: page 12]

4x HE10, 2x HE5

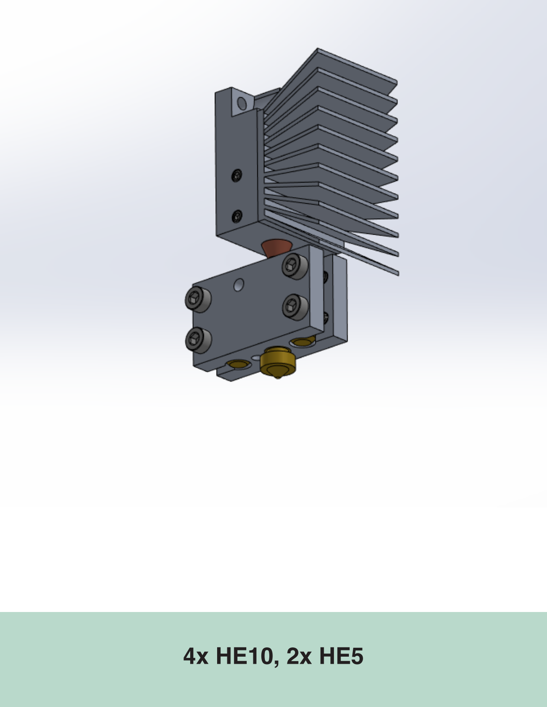
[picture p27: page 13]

4x HE10, 2x HE5

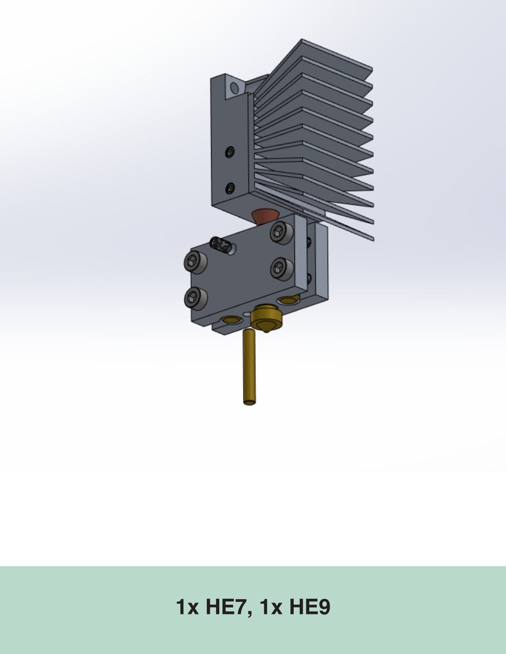
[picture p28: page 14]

1x HE7, 1x HE9

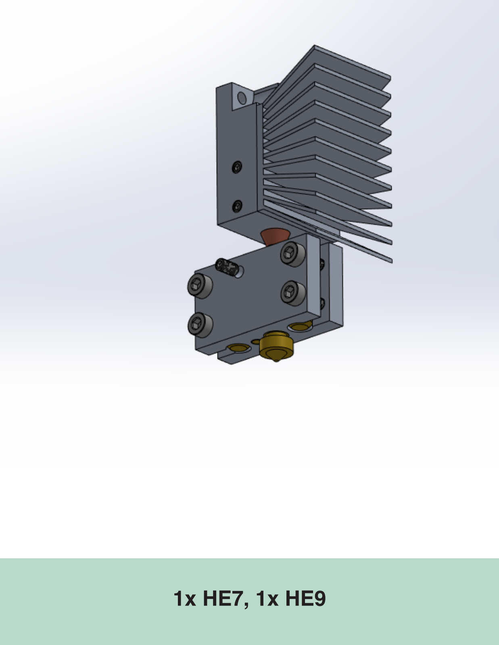
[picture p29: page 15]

1x HE7, 1x HE9

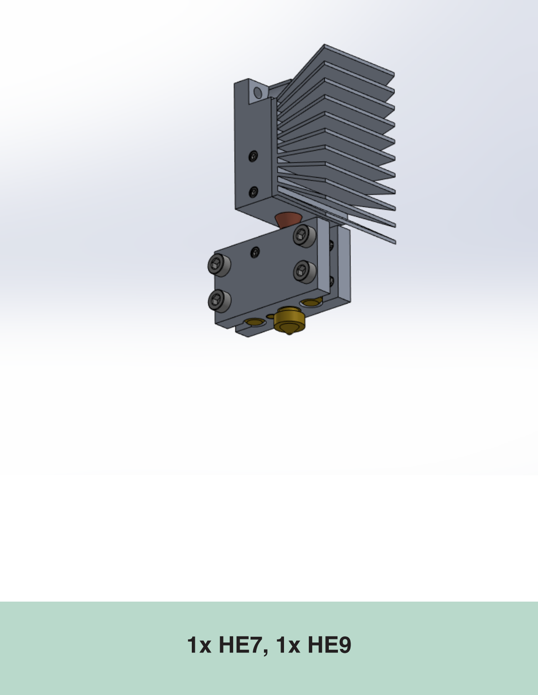
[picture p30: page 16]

1x HE7, 1x HE9

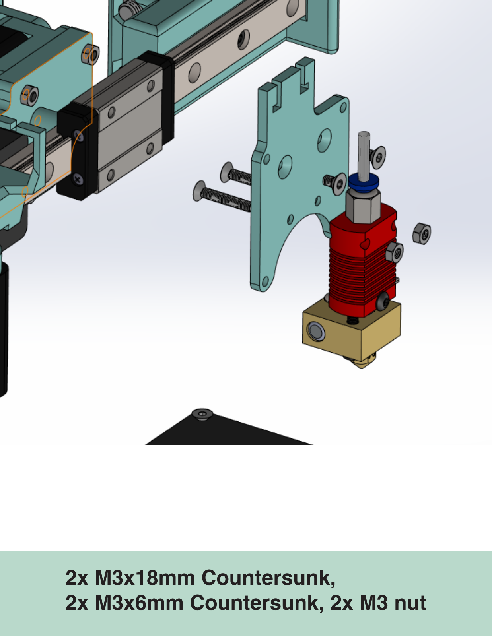
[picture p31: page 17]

2x M3x18mm Countersunk,
2x M3x6mm Countersunk, 2x M3 nut

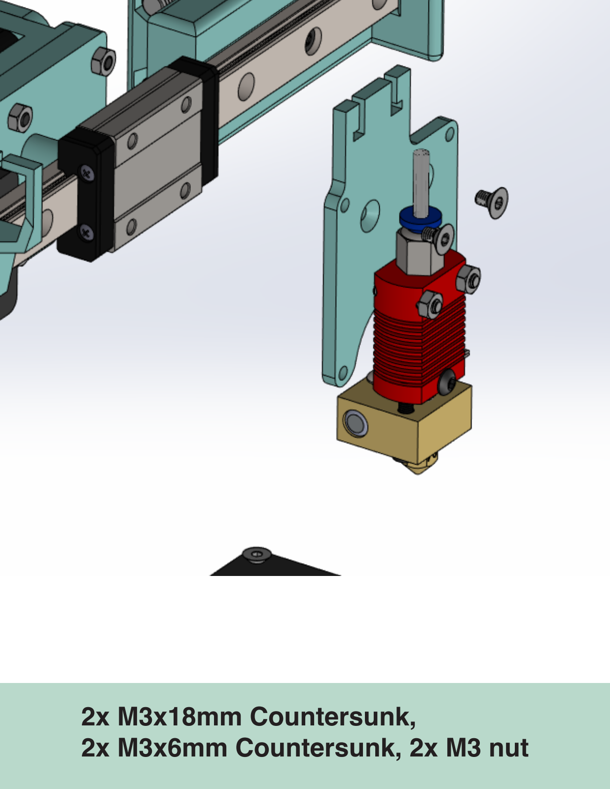
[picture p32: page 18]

2x M3x18mm Countersunk,
2x M3x6mm Countersunk, 2x M3 nut

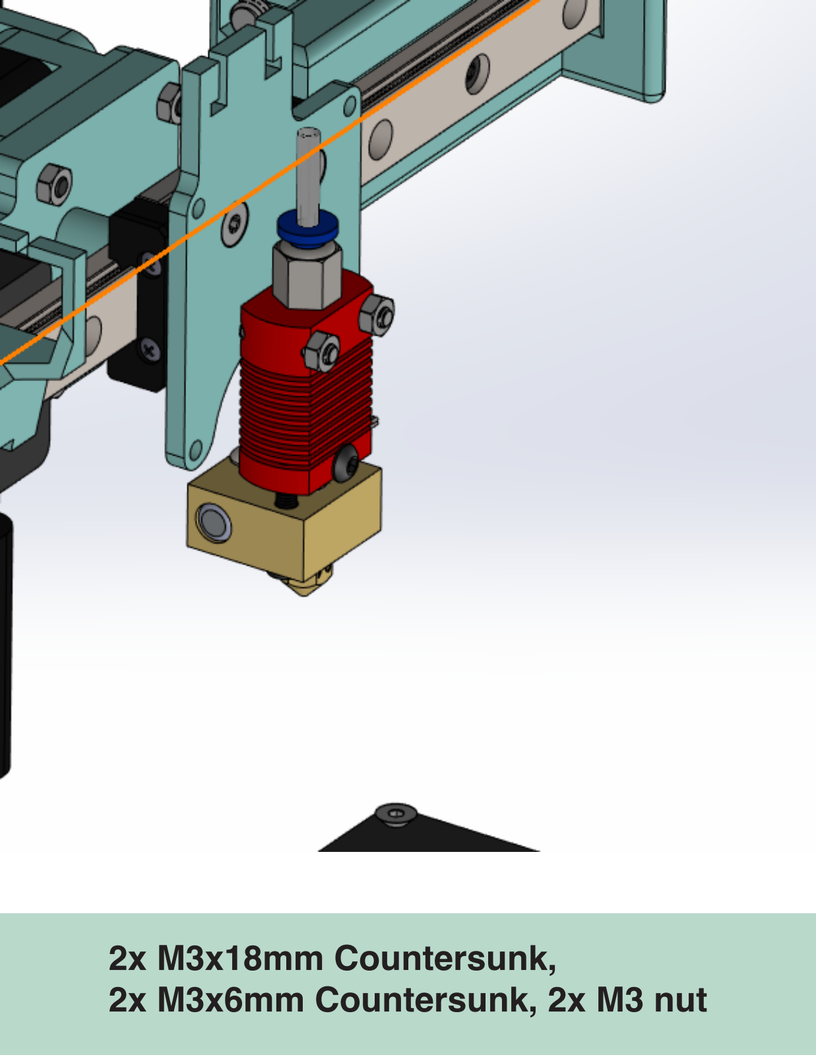
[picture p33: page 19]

2x M3x18mm Countersunk,
2x M3x6mm Countersunk, 2x M3 nut

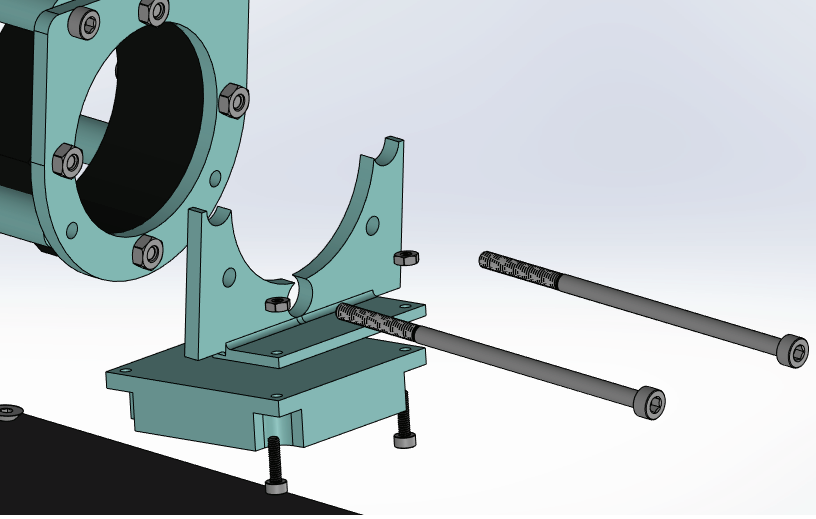
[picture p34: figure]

2x M2x8mm, 2x M3x70mm, 2x M2 nut

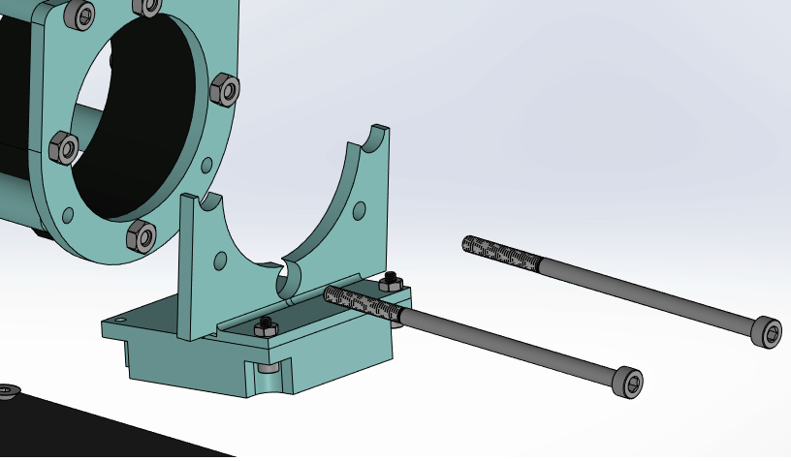
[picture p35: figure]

2x M2x8mm, 2x M3x70mm, 2x M2 nut

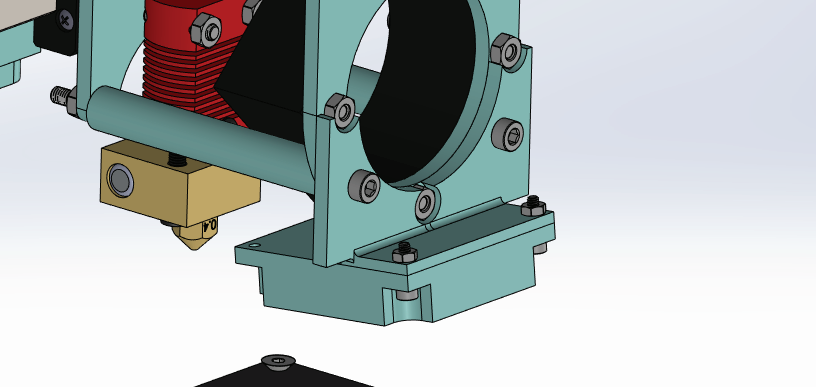
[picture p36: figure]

2x M2x8mm, 2x M3x70mm, 2x M2 nut

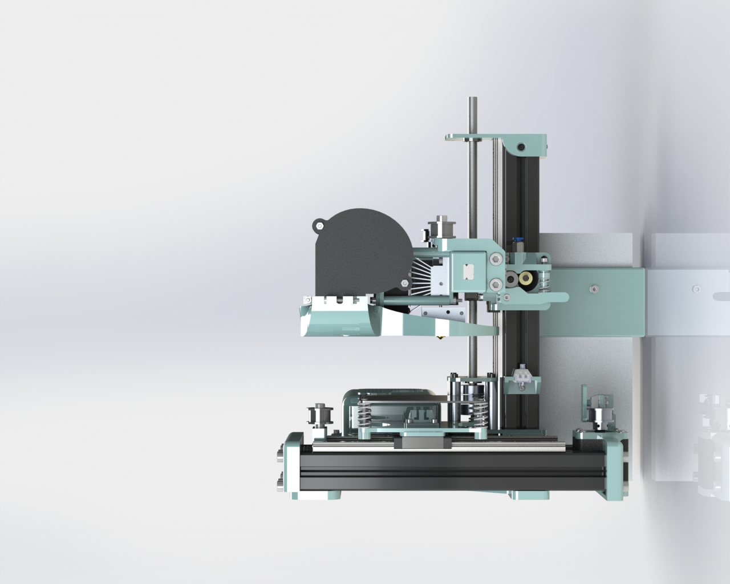
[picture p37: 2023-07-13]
FullCADRenders/PrinterRightView.JPG

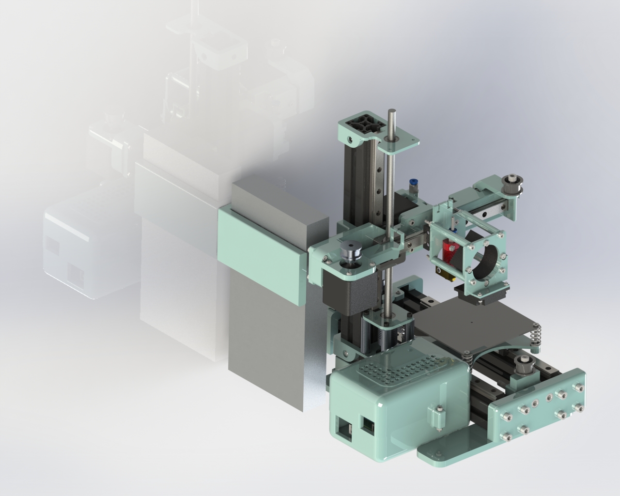
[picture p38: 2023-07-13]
FullCADRenders/PrinterEnder3HotEndView.JPG

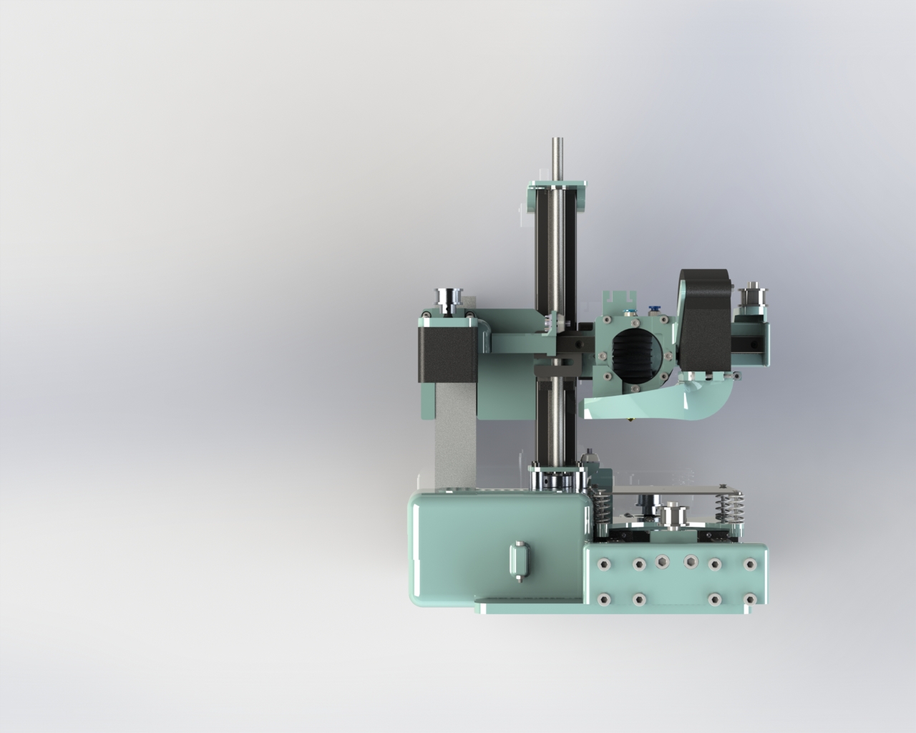
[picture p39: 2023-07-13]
FullCADRenders/PrinterFrontView.JPG

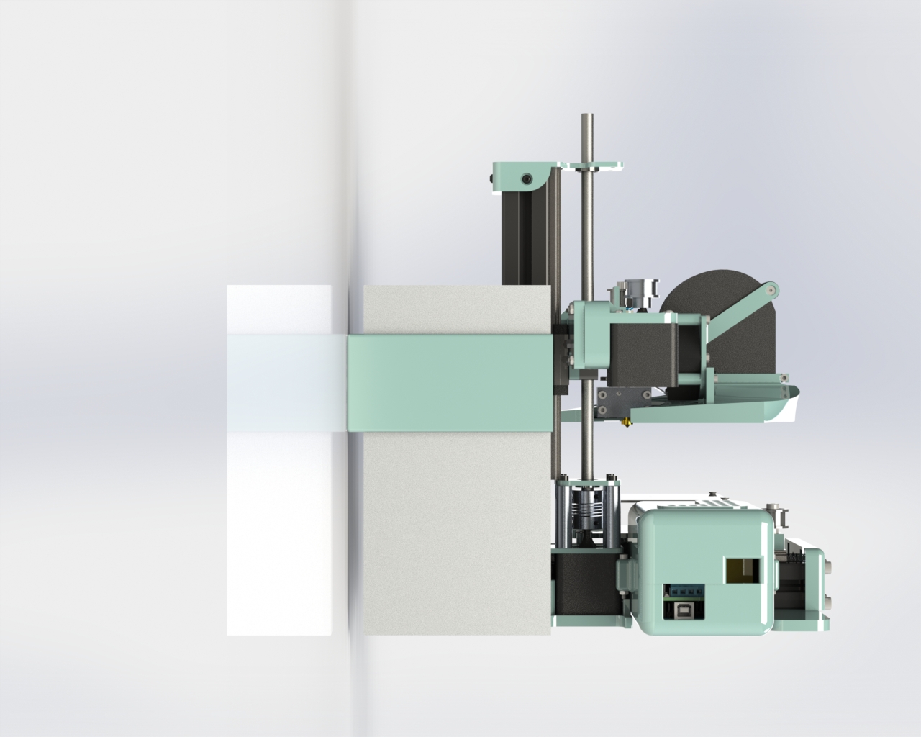
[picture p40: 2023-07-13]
FullCADRenders/PrinterLeftView.JPG

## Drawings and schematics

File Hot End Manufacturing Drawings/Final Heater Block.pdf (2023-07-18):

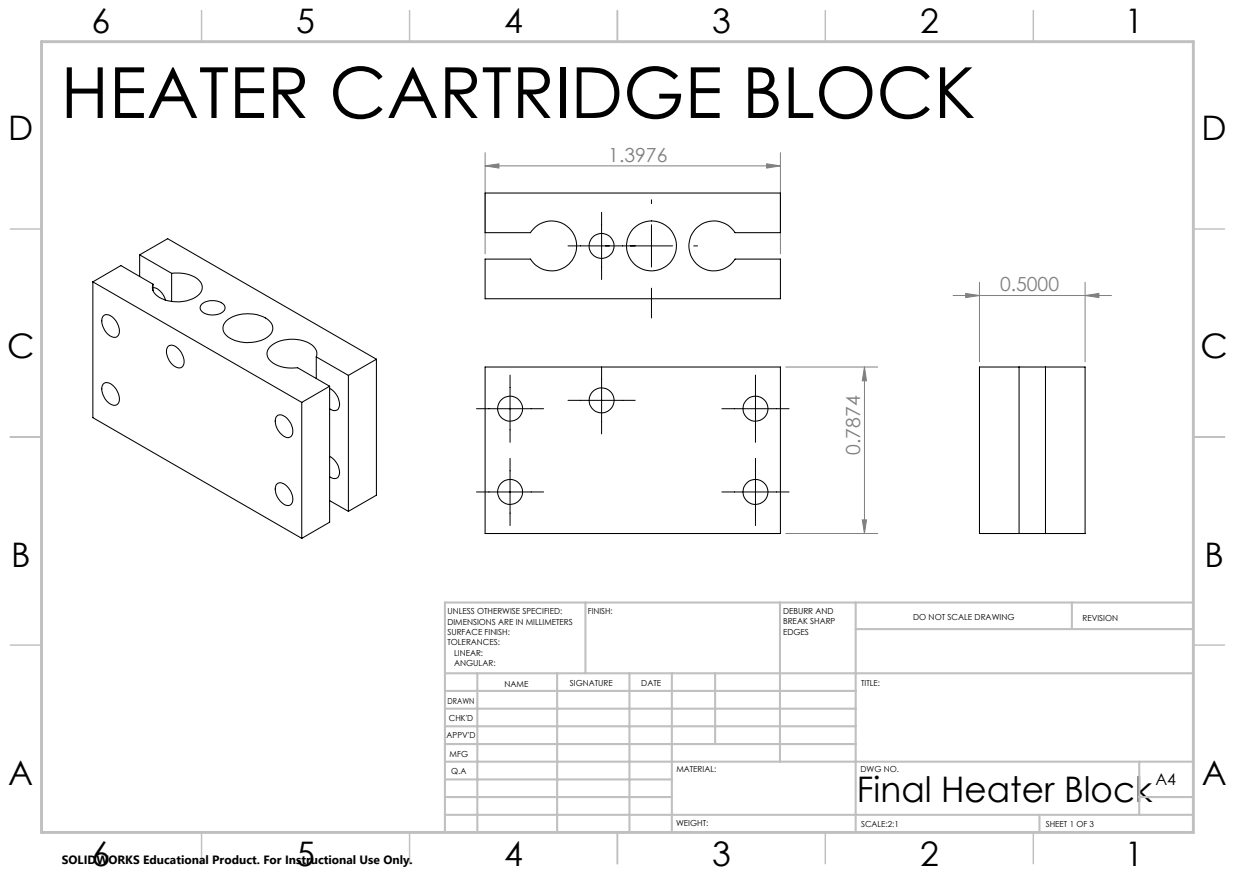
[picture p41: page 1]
FINISH:; DEBURR AND; BREAK SHARP; DO NOT SCALE DRAWING; REVISION; SCALE:2:1; SHEET 1 OF 3

HEATER CARTRIDGE BLOCK

UNLESS OTHERWISE SPECIFIED:
DIMENSIONS ARE IN MILLIMETERS
SURFACE FINISH:
TOLERANCES:
LINEAR:
ANGULAR:

NAME | SIGNATURE | DATE | | | | TITLE:

DRAWN
CHK'D
APPV'D
MFG
Q.A | | | | MATERIAL: | DWG NO. Final Heater Block | A4

SOLIDWORKS Educational Product. For Instructional Use Only.

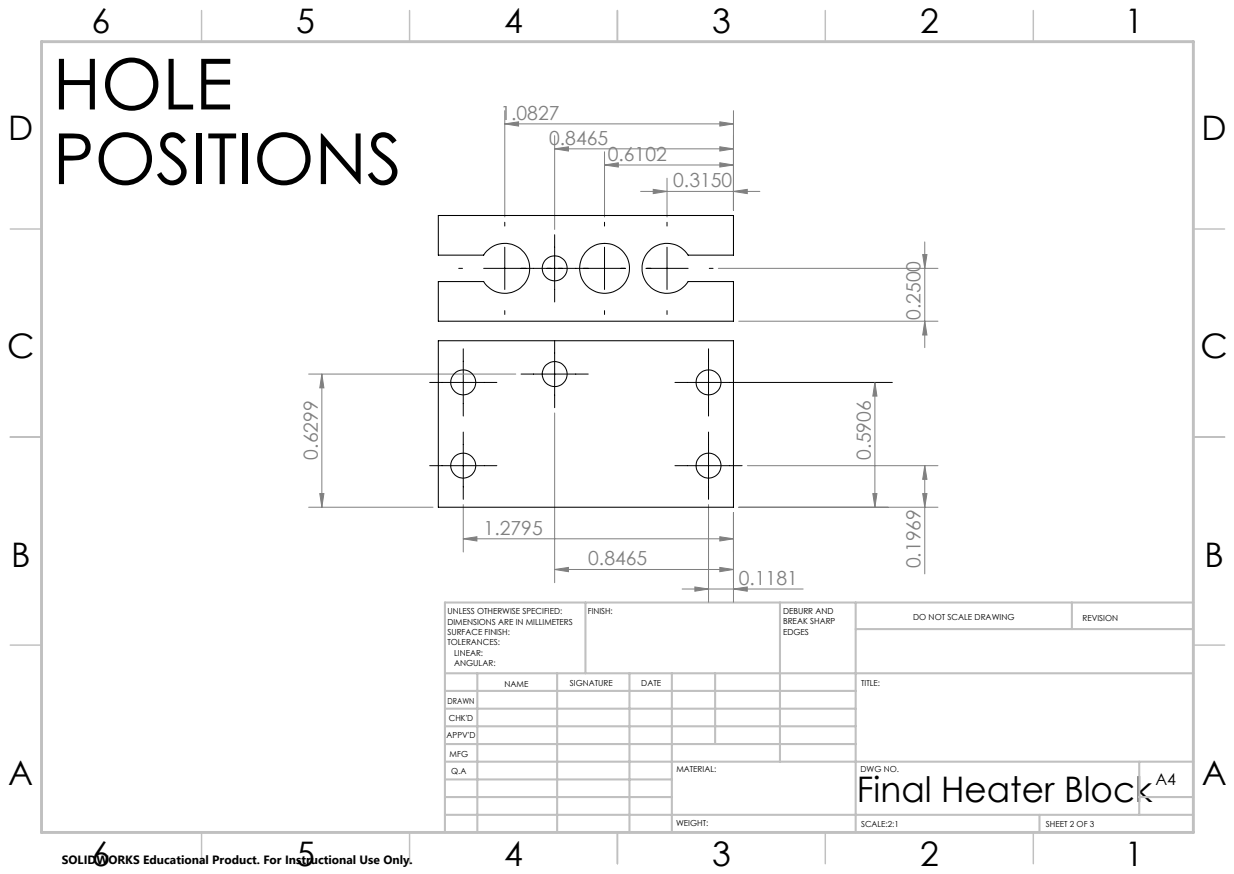
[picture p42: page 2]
FINISH:; DEBURR AND; BREAK SHARP; DO NOT SCALE DRAWING; REVISION

0.8465
0.6102

UNLESS OTHERWISE SPECIFIED:
DIMENSIONS ARE IN MILLIMETERS
SURFACE FINISH:
TOLERANCES:
LINEAR:
ANGULAR:

NAME | SIGNATURE | DATE | | | | TITLE:

DRAWN
CHK'D
APPV'D
MFG
Q.A | | | | MATERIAL: | DWG NO. Final Heater Block | A4

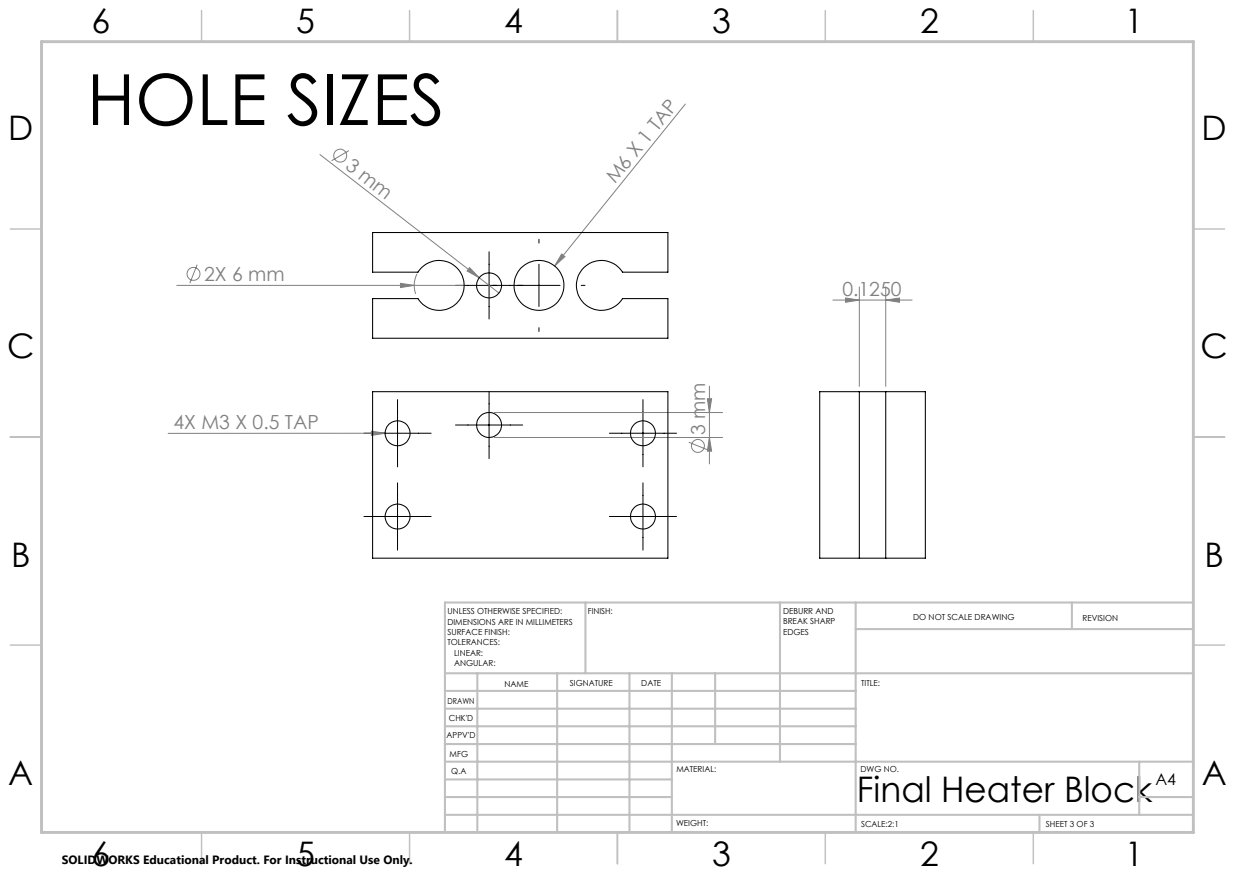
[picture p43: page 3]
4X M3 X 0.5 TAP; M6 X 1 TAP; HOLE SIZES; FINISH:; DEBURR AND; BREAK SHARP; DO NOT SCALE DRAWING; REVISION

UNLESS OTHERWISE SPECIFIED:
DIMENSIONS ARE IN MILLIMETERS
SURFACE FINISH:
TOLERANCES:
LINEAR:
ANGULAR:

NAME | SIGNATURE | DATE | | | | TITLE:

DRAWN
CHK'D
APPV'D
MFG
Q.A | | | | MATERIAL: | DWG NO. Final Heater Block | A4

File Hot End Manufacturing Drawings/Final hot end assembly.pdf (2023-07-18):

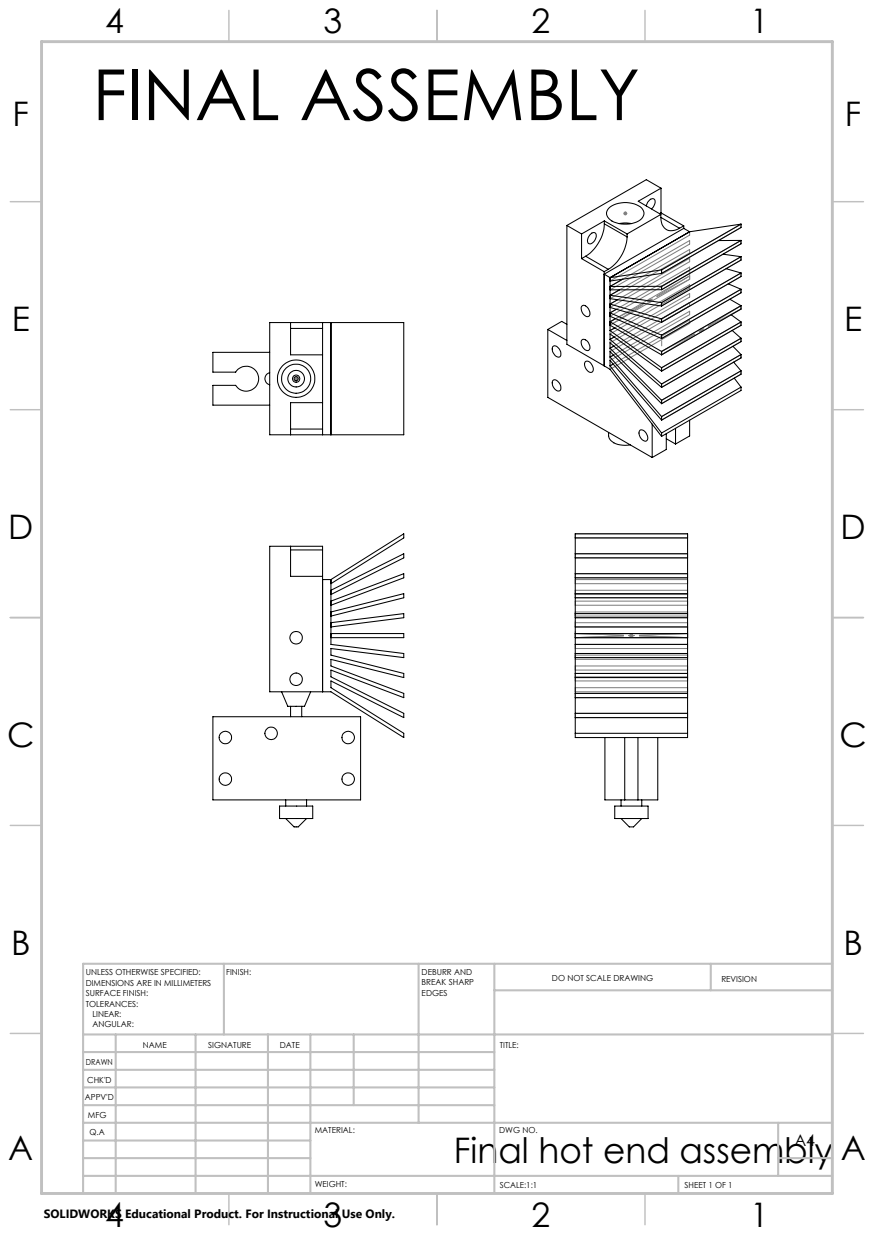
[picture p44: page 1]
FINAL ASSEMBLY; FINISH:; DEBURR AND; BREAK SHARP; DO NOT SCALE DRAWING; REVISION; SCALE:1:1; SHEET 1 OF 1

UNLESS OTHERWISE SPECIFIED:
DIMENSIONS ARE IN MILLIMETERS
SURFACE FINISH:
TOLERANCES:
LINEAR:
ANGULAR:

NAME | SIGNATURE | DATE | | | | TITLE:

DRAWN
CHK'D
APPV'D
MFG
Q.A | | | | MATERIAL: Final hot end assembly | DWG NO. | A4

SOLIDWORKS Educational Product. For Instructional Use Only.

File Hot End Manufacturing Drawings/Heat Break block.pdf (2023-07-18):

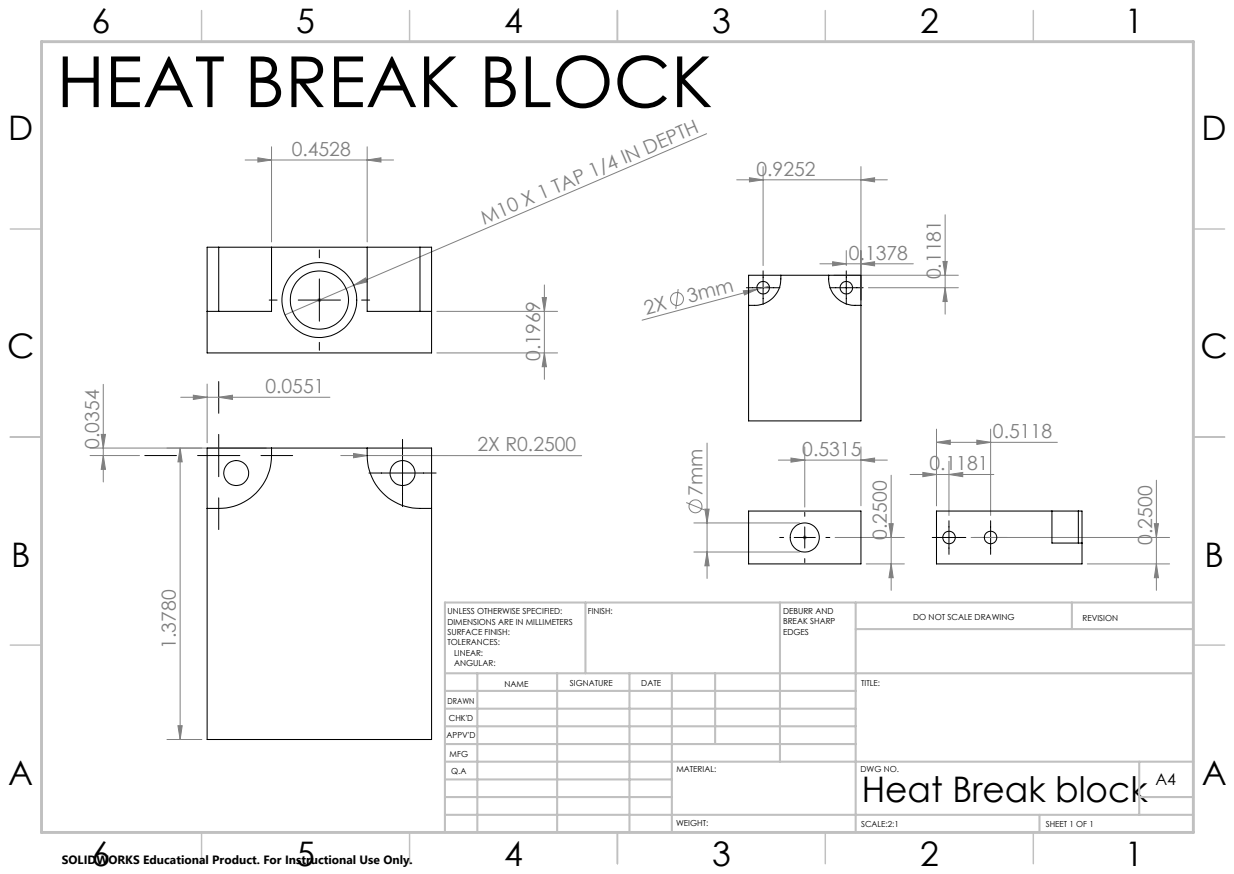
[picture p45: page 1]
M10 X 1 TAP 1/4 IN DEPTH; FINISH:; DEBURR AND; BREAK SHARP; DO NOT SCALE DRAWING; REVISION; SCALE:2:1; SHEET 1 OF 1

HEAT BREAK BLOCK

UNLESS OTHERWISE SPECIFIED:
DIMENSIONS ARE IN MILLIMETERS
SURFACE FINISH:
TOLERANCES:
LINEAR:
ANGULAR:

NAME | SIGNATURE | DATE | | | | TITLE:

DRAWN
CHK'D
APPV'D
MFG
Q.A | | | | MATERIAL: | DWG NO. Heat Break block | A4

SOLIDWORKS Educational Product. For Instructional Use Only.

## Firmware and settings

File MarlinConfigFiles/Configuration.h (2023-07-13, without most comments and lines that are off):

#pragma once
#define CONFIGURATION_H_VERSION 02010300
#define STRING_CONFIG_H_AUTHOR "(none, default config)" // Who made the changes.
#define SHOW_BOOTSCREEN
  #define MOTHERBOARD BOARD_RAMPS_14_EEB
#define SERIAL_PORT 0
#define BAUDRATE 250000
#define CUSTOM_MACHINE_NAME "Angel"//AH
#define MACHINE_UUID "a3b4d936-84f4-4481-827e-e710c23f43a9"//AH
#define X_DRIVER_TYPE  DRV8825//AH
#define Y_DRIVER_TYPE  DRV8825//AH
#define Z_DRIVER_TYPE  DRV8825//AH
#define E0_DRIVER_TYPE DRV8825//AH
#define EXTRUDERS 1
#define DEFAULT_NOMINAL_FILAMENT_DIA 1.75
#define TEMP_SENSOR_0 5//AH
#define TEMP_SENSOR_BED 1000//AH
#define DUMMY_THERMISTOR_998_VALUE  25
#define DUMMY_THERMISTOR_999_VALUE 100
#if TEMP_SENSOR_IS_MAX_TC(0)
  #define MAX31865_SENSOR_OHMS_0      100 // (Ω) Typically 100 or 1000 (PT100 or PT1000)
  #define MAX31865_CALIBRATION_OHMS_0 430 // (Ω) Typically 430 for Adafruit PT100; 4300 for Adafruit PT1000
#endif
#if TEMP_SENSOR_IS_MAX_TC(1)
  #define MAX31865_SENSOR_OHMS_1      100
  #define MAX31865_CALIBRATION_OHMS_1 430
#endif
#if TEMP_SENSOR_IS_MAX_TC(2)
  #define MAX31865_SENSOR_OHMS_2      100
  #define MAX31865_CALIBRATION_OHMS_2 430
#endif
#if HAS_E_TEMP_SENSOR
  #define TEMP_RESIDENCY_TIME         10  // (seconds) Time to wait for hotend to "settle" in M109
  #define TEMP_WINDOW                  1  // (°C) Temperature proximity for the "temperature reached" timer
  #define TEMP_HYSTERESIS              3  // (°C) Temperature proximity considered "close enough" to the target
#endif
#if TEMP_SENSOR_BED
  #define TEMP_BED_RESIDENCY_TIME     10  // (seconds) Time to wait for bed to "settle" in M190
  #define TEMP_BED_WINDOW              1  // (°C) Temperature proximity for the "temperature reached" timer
  #define TEMP_BED_HYSTERESIS          3  // (°C) Temperature proximity considered "close enough" to the target
#endif
#if TEMP_SENSOR_CHAMBER
  #define TEMP_CHAMBER_RESIDENCY_TIME 10  // (seconds) Time to wait for chamber to "settle" in M191
  #define TEMP_CHAMBER_WINDOW          1  // (°C) Temperature proximity for the "temperature reached" timer
  #define TEMP_CHAMBER_HYSTERESIS      3  // (°C) Temperature proximity considered "close enough" to the target
#endif
#if TEMP_SENSOR_REDUNDANT
  #define TEMP_SENSOR_REDUNDANT_SOURCE    E1  // The sensor that will provide the redundant reading.
  #define TEMP_SENSOR_REDUNDANT_TARGET    E0  // The sensor that we are providing a redundant reading for.
  #define TEMP_SENSOR_REDUNDANT_MAX_DIFF  10  // (°C) Temperature difference that will trigger a print abort.
#endif
#define HEATER_0_MINTEMP   5
#define HEATER_1_MINTEMP   5
#define HEATER_2_MINTEMP   5
#define HEATER_3_MINTEMP   5
#define HEATER_4_MINTEMP   5
#define HEATER_5_MINTEMP   5
#define HEATER_6_MINTEMP   5
#define HEATER_7_MINTEMP   5
#define BED_MINTEMP        5
#define CHAMBER_MINTEMP    5
#define HEATER_0_MAXTEMP 275
#define HEATER_1_MAXTEMP 275
#define HEATER_2_MAXTEMP 275
#define HEATER_3_MAXTEMP 275
#define HEATER_4_MAXTEMP 275
#define HEATER_5_MAXTEMP 275
#define HEATER_6_MAXTEMP 275
#define HEATER_7_MAXTEMP 275
#define BED_MAXTEMP      150
#define CHAMBER_MAXTEMP  60
#define HOTEND_OVERSHOOT 15   // (°C) Forbid temperatures over MAXTEMP - OVERSHOOT
#define BED_OVERSHOOT    10   // (°C) Forbid temperatures over MAXTEMP - OVERSHOOT
#define COOLER_OVERSHOOT  2   // (°C) Forbid temperatures closer than OVERSHOOT
#define PIDTEMP          // See the PID Tuning Guide at https://reprap.org/wiki/PID_Tuning
#define BANG_MAX 255     // Limits current to nozzle while in bang-bang mode; 255=full current
#define PID_MAX BANG_MAX // Limits current to nozzle while PID is active (see PID_FUNCTIONAL_RANGE below); 255=full current
#define PID_K1 0.95      // Smoothing factor within any PID loop
    #define DEFAULT_Kp 19.85//AH
    #define DEFAULT_Ki 1.44//AH
    #define DEFAULT_Kd 68.29//AH
#define PIDTEMPBED
#define MAX_BED_POWER 235 // limits duty cycle to bed; 255=full current//AH
  #define DEFAULT_bedKp 59.47//AH
  #define DEFAULT_bedKi 11.71//AH
  #define DEFAULT_bedKd 201.37//AH
#define MAX_CHAMBER_POWER 255 // limits duty cycle to chamber heater; 255=full current
  #define PID_FUNCTIONAL_RANGE 10 // If the temperature difference between the target temperature and the actual temperature
#define PREVENT_COLD_EXTRUSION
#define EXTRUDE_MINTEMP 170
#define PREVENT_LENGTHY_EXTRUDE
#define EXTRUDE_MAXLENGTH 200
#define THERMAL_PROTECTION_HOTENDS // Enable thermal protection for all extruders
#define THERMAL_PROTECTION_BED     // Enable thermal protection for the heated bed
#define THERMAL_PROTECTION_CHAMBER // Enable thermal protection for the heated chamber
#define THERMAL_PROTECTION_COOLER  // Enable thermal protection for the laser cooling
#define USE_XMIN_PLUG
#define USE_YMIN_PLUG//AH
#define USE_ZMIN_PLUG
#define ENDSTOPPULLUPS
#define X_MIN_ENDSTOP_INVERTING true // Set to true to invert the logic of the endstop. AH
#define Y_MIN_ENDSTOP_INVERTING true // Set to true to invert the logic of the endstop.
#define Z_MIN_ENDSTOP_INVERTING true // Set to true to invert the logic of the endstop. AH
#define I_MIN_ENDSTOP_INVERTING false // Set to true to invert the logic of the endstop.
#define J_MIN_ENDSTOP_INVERTING false // Set to true to invert the logic of the endstop.
#define K_MIN_ENDSTOP_INVERTING false // Set to true to invert the logic of the endstop.
#define U_MIN_ENDSTOP_INVERTING false // Set to true to invert the logic of the endstop.
#define V_MIN_ENDSTOP_INVERTING false // Set to true to invert the logic of the endstop.
#define W_MIN_ENDSTOP_INVERTING false // Set to true to invert the logic of the endstop.
#define X_MAX_ENDSTOP_INVERTING false // Set to true to invert the logic of the endstop.
#define Y_MAX_ENDSTOP_INVERTING true // Set to true to invert the logic of the endstop. AH
#define Z_MAX_ENDSTOP_INVERTING false // Set to true to invert the logic of the endstop.
#define I_MAX_ENDSTOP_INVERTING false // Set to true to invert the logic of the endstop.
#define J_MAX_ENDSTOP_INVERTING false // Set to true to invert the logic of the endstop.
#define K_MAX_ENDSTOP_INVERTING false // Set to true to invert the logic of the endstop.
#define U_MAX_ENDSTOP_INVERTING false // Set to true to invert the logic of the endstop.
#define V_MAX_ENDSTOP_INVERTING false // Set to true to invert the logic of the endstop.
#define W_MAX_ENDSTOP_INVERTING false // Set to true to invert the logic of the endstop.
#define Z_MIN_PROBE_ENDSTOP_INVERTING false // Set to true to invert the logic of the probe.
#define ENDSTOP_INTERRUPTS_FEATURE//AH
#define DEFAULT_AXIS_STEPS_PER_UNIT   { 106.6, 106.6, 789.2, 203 } //AH
#define DEFAULT_MAX_FEEDRATE          { 300, 300, 5, 25 }
#define DEFAULT_MAX_ACCELERATION      { 3000, 3000, 100, 10000 }
#define DEFAULT_ACCELERATION          3000    // X, Y, Z and E acceleration for printing moves
#define DEFAULT_RETRACT_ACCELERATION  3000    // E acceleration for retracts
#define DEFAULT_TRAVEL_ACCELERATION   3000    // X, Y, Z acceleration for travel (non printing) moves
#define DEFAULT_EJERK    5.0  // May be used by Linear Advance
  #define JUNCTION_DEVIATION_MM 0.013 // (mm) Distance from real junction edge
  #define JD_HANDLE_SMALL_SEGMENTS    // Use curvature estimation instead of just the junction angle
#define Z_MIN_PROBE_USES_Z_MIN_ENDSTOP_PIN
#define NOZZLE_TO_PROBE_OFFSET { 10, 10, 0 }
#define PROBING_MARGIN 10
#define XY_PROBE_FEEDRATE (133*60)
#define Z_PROBE_FEEDRATE_FAST (4*60)
#define Z_PROBE_FEEDRATE_SLOW (Z_PROBE_FEEDRATE_FAST / 2)
#define Z_CLEARANCE_DEPLOY_PROBE   10 // Z Clearance for Deploy/Stow
#define Z_CLEARANCE_BETWEEN_PROBES  5 // Z Clearance between probe points
#define Z_CLEARANCE_MULTI_PROBE     5 // Z Clearance between multiple probes
#define Z_PROBE_LOW_POINT          -2 // Farthest distance below the trigger-point to go before stopping
#define Z_PROBE_OFFSET_RANGE_MIN -20
#define Z_PROBE_OFFSET_RANGE_MAX 20
#define X_ENABLE_ON 0
#define Y_ENABLE_ON 0
#define Z_ENABLE_ON 0
#define E_ENABLE_ON 0 // For all extruders
#define DISABLE_X false
#define DISABLE_Y false
#define DISABLE_Z false
#define DISABLE_E false             // Disable the extruder when not stepping
#define DISABLE_INACTIVE_EXTRUDER   // Keep only the active extruder enabled
#define INVERT_X_DIR false
#define INVERT_Y_DIR true
#define INVERT_Z_DIR false
#define INVERT_E0_DIR false
#define INVERT_E1_DIR false
#define INVERT_E2_DIR false
#define INVERT_E3_DIR false
#define INVERT_E4_DIR false
#define INVERT_E5_DIR false
#define INVERT_E6_DIR false
#define INVERT_E7_DIR false
#define X_HOME_DIR -1
#define Y_HOME_DIR -1
#define Z_HOME_DIR -1
#define X_BED_SIZE 80//AH
#define Y_BED_SIZE 100//AH
#define X_MIN_POS -10//AH
#define Y_MIN_POS -13//AH
#define Z_MIN_POS 0//AH
#define X_MAX_POS 89//AH
#define Y_MAX_POS 104//AH
#define Z_MAX_POS 100//AH
#define MIN_SOFTWARE_ENDSTOPS
  #define MIN_SOFTWARE_ENDSTOP_X
  #define MIN_SOFTWARE_ENDSTOP_Y
  #define MIN_SOFTWARE_ENDSTOP_Z
  #define MIN_SOFTWARE_ENDSTOP_I
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

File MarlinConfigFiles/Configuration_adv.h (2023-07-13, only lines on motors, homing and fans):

#define E0_AUTO_FAN_PIN -1
#define E1_AUTO_FAN_PIN -1
#define E2_AUTO_FAN_PIN -1
#define E3_AUTO_FAN_PIN -1
#define E4_AUTO_FAN_PIN -1
#define E5_AUTO_FAN_PIN -1
#define E6_AUTO_FAN_PIN -1
#define E7_AUTO_FAN_PIN -1
#define CHAMBER_AUTO_FAN_PIN -1
#define COOLER_AUTO_FAN_PIN -1
#define HOMING_BUMP_MM      { 5, 5, 2 }       // (linear=mm, rotational=°) Backoff from endstops after first bump
#define HOMING_BUMP_DIVISOR { 2, 2, 4 }       // Re-Bump Speed Divisor (Divides the Homing Feedrate)
#define MICROSTEP_MODES { 16, 16, 16, 16, 16, 16 } // [1,2,4,8,16]
#define LIN_ADVANCE//AH
    #define ADVANCE_K 0.16 //AH        // (mm) Compression length applying to all extruders

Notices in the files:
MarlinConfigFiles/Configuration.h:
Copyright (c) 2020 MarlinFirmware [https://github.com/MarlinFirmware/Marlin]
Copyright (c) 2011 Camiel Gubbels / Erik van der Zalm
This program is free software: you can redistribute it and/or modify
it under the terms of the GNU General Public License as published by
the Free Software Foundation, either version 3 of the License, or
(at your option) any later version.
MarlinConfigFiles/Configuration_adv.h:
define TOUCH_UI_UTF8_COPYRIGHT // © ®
